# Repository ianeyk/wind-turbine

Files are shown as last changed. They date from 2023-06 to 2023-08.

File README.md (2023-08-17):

# wind-turbine
Working repo for summer research on the Just Energy Hub wind turbine design.

## GitHub Repo Index
* **Small_wind_turbine**
    * **3_phase_generator_buck_converter.plecs:** Main working PLECS model for the small turbine buck converter
    * **Frequency_analysis_buck_converter**
        * Contains four additional PLECS models which were used to run bode plots for designing the compensator circuit for the small wind turbine.
    * **Small_turbine_buck_converter_parameters**
        * **Buck_converter_parameters.ipynb:** Jupyter Notebook containing calculations for the inductor value and compensator circuit.
        * **Buck_converter_parameters.html:** Exported HTML of same Notebook
        * **Buck_converter_parameters.pdf:** Exported PDF of same Notebook
        * **Plecs_helper.py:** Library of helper functions used in the Notebook
    * **Small_buck_converter_design_calculations**
        * **Design_calculations.ipynb, html, pdf:** Secondary notebook for calculating such things as how much current the turbine can supply at safe rotation speeds, specs for the input capacitance value, slew rate to ensure the diff amps can respond fast enough, and resistor values for the indicator LEDs.
    * **KiCAD:** Contains the schematic and layout for the small-scale buck converter PCB board which I designed and manufactured over the summer.
* **Large_wind_turbine**
    * **siemens_model_buck_converter_v1.plecs:** Main working PLECS model for the large turbine buck converter, including the 1FW3208-1EE model of the physical generator. The only things that are different between this model and the small_wind_turbine model are the inductor value, compensator values, and perhaps the input capacitance.
     * **1_kv_3phase_generator_buck_converter.plecs:** Older model without using the 1FW3208-1EE model.
    * **Frequency_analysis_buck_converter**
        * Contains four additional PLECS models which were used to run bode plots for designing the compensator circuit for the large wind turbine.
    * **Large_turbine_buck_converter_parameters**
        * **Buck_converter_parameters.ipynb:** Jupyter Notebook containing calculations for the inductor value and compensator circuit.
        * **Minimum_conversion_ratio.ipynb:** Jupyter Notebook containing calculations for the minimum switching time given a 1kV-12V buck converter voltage ratio. I concluded that this is perfectly feasible given a 10kHz switching frequency.
    * **KiCAD:** Folder containing duplicates of the small wind turbine KiCAD files. I was going to start with a copy and modify it, but I never got around to starting it.
    * **LTspice:** Contains a single LTspice model verifying that the bootstrap gate driver will work.
* **Generic_wind_turbine**
    * Earlier exploratory work which served as a template for the above analyses. It should probably be moved to the Archive folder.
* **Measurements_and_calculations**
    * **Battery_measurements**
        * **Battery_resistance.ipynb, .html, .pdf:** Jupyter Notebook analyzing a small set of data I took on our 12V marine batteries in the lab to quantify the internal resistance.
    * **Generator_volage**
        * **Generator_voltage.ipynb, .html, .pdf:** Jupyter Notebook plotting the results of putting the small test turbine in front of the wind tunnel. It calculates the frequency and voltage amplitude at various wind speeds.
    * **Large_turbine_power_predictions**
        * **Large_turbine_power_predictions.ipyny, .html, .pdf:** Jupyter Notebook and exported versions analyzing the power generation data from one of the Eastern Wind Power documents as well as a PLECS model for the generator and the anemometer data from Olin's campus. I recommend a cut-out wind speed of 12m/s for the large turbine.
* **Charge_controller_code**
    * **Platformio.ini:** Platformio project for code running on the Adafruit Feather Adalogger board attached to the small-scale buck converter PCB I designed and manufactured this summer.
    * **src/main.cpp:** Main code file containing Arduino language to be uploaded to the Feather.
* **Archive**
    * **Generator_internal_resistance**
        * **Internal_resistance.ipynb, .html, .pdf:** Jupyter Notebook for an initial experiment determining the internal resistance of the small generator by hand-spinning the small turbine and watching the frequency and voltage decay as it slowed down. The internal resistance calculations match those in *Generator_voltage.ipynb*, and that notebook also has further relevant calculations. Hence this notebook is in the archive.

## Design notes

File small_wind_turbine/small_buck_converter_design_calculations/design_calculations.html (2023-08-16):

# Small Buck Converter Design Calculations¶

Author: Ian Eykamp, Date: 6/16/2023

## Purpose¶

To document certain calculations for the design of the small wind turbine buck converter, including

- Maximum output current
- Input capacitor size
- Slew rate of current wafeforms for speccing diff amps
- Indicator LED resistances

### Import libraries¶

plecs_helper.py is a file I created which defines some helper functions for nice plots and getting data off the oscilloscope and out of PLECS.

In [ ]:

import numpy as np
import pandas as pd
import matplotlib.pyplot as plt
import matplotlib.ticker as mtick
from UliEngineering.EngineerIO import format_value
from si_prefix import si_format
import plecs_helper as helper
%matplotlib
%matplotlib inline

# Imports and setup
from pint import UnitRegistry, Quantity
from scipy.signal import find_peaks
from scipy.optimize import fsolve

# pandas display using scientific notation
# pd.set_option('display.float_format', lambda x: f'{x:.3e}')

# use pint
units = UnitRegistry()
units.default_format = "~P.2f"

def to_decibels(arr, dc_gain = 0):
    return np.log10(np.abs(arr)) * 20 + dc_gain

Using matplotlib backend: TkAgg

## Calculating maximum current¶

The buck converter will draw a certain average current from the rectifier; in doing so, it produces a known output voltage (the battery voltage, which may be between 12V and 14.6V) and a known output current. The buck converter acts like an ideal transformer in that it preserves the product of voltage and amperage from the input to the output, $P_{in} = V_{in} \cdot I_{in} = V_{out} \cdot I_{out} = P_{out}$. The input voltage is the voltage between the terminals of the rectifier. Using this, we can calculate $I_{in} = V_{out} \cdot I_{out} / V_{in}$. Once we have $I_{in}$, we can calculate the voltage drop across the internal resistance of the generator by $V = IR$. I will call this $\Delta V_{internal}$. The voltage now available for the buck converter to use is $V_{in} = V_{gen} - \Delta V_{internal}$. So, depending on how much output current we want to draw into the battery, it will affect the voltage available at the buck converter input.

We need to charge a 12V battery (really, when it’s done charging, it will be at 14.6V) using our buck converter. Because of the chip we are using, our buck converter can have no more than a 50% duty cycle, which means our input voltage must be at least $2 \cdot 14.6V = 29.2V$ at a bare minimum. Round up to $V_{in} = 30V$ at a minimum.

To spin the generator and get power out of it, I will place it in front of the 4th floor wind tunnel in the Rocketry lab. Without getting to a point where I felt it was dangerous, I can get it to 30V with a 100Ω load resistance. I am confident I can spin it faster if we need a higher voltage; in fact, I made my design with 50V or higher in mind.

We know our voltage divider has to give us at least 30V from the 50V available. That means there can be no more than a 20V drop across the 14.5Ω internal resistance, which corresponds with a 1.3A current through the rectifier.

We have $I_{in} = 1.3A$, $V_{in} = 30V$, $V_{out} = 14.6V$, and $V_{in} \cdot I_{in} = V_{out} \cdot I_{out}$. Thus, the maximum current we can safely draw for a 50V generator voltage is 2.8A. Likely, the available current to the battery would be much smaller because the power converter is not 100% efficient (in fact 70% or 80% efficiency is a fairly good design) and because there are many auxiliary IC’s and the microcontroller that will eat up a lot of the excess current.

Well, I guess I’ll just keep our current down between 0 and 0.5A to be safe. (Just kidding, I already designed the thing with a maximum of 0.5A in mind, and I don't want to redo all the analysis after realizing that 1A or more would be fine).

In [ ]:

Vout = 14.6 * units.volt # battery voltage
Rinternal = 14.5 * units.ohm
Vgen = 50 * units.volt
Vin = 30 * units.volt
Vinternal = Vgen - Vin
Iin = Vinternal / Rinternal
Iout = Iin * Vin / Vout
print(f"Assuming Vgen = 50V, we have Iout = {Iout.to_compact(units.amp)}")

Assuming Vgen = 50V, we have Iout = 2.83 A

At 0.5A of output current, it would take only 35V at the generator, or actually probably closer to 40V because of the inefficiencies.

In [ ]:

Vout = 14.6 * units.volt # battery voltage
Rinternal = 14.5 * units.ohm
Vin = 30 * units.volt
Iout = 0.5 * units.amp + 0.5 * units.amp
Vgen = Vin + Iout * Vout / Vin * Rinternal
print(f"Assuming Iout = 0.5A, with another 0.5A for auxiliary components, we need Vgen = {Vgen.to_compact(units.volt)}")

Assuming Iout = 0.5A, with another 0.5A for auxiliary components, we need Vgen = 37.06 V

## Calculating Input Capacitance¶

This averaged transformer analysis has all been made possible by assuming the input voltage does not change in response to the switching

We have been calculating using the average input and output currents. For the buck converter to work properly, it needs to satisfy the input voltage even at the moment of peak current draw. In boundary conduction mode (BCM) where we are nominally operating, the peak current is two times the average current. For higher currents, we will go into continuous conduction mode (CCM), where the peak current is slightly less than twice the average current; for lower currents, we will go into discontinuous conduction mode (DCM) and require more than twice the average current at the peak.

Fortunately, if we have a big enough input capacitor, then we can smooth out the current waveform and almost exclusively care about the average current. By $I = C \frac{dV}{dt}$, there is always some voltage drop at the Vin node when the extra current is being sourced by the capacitor, but by choosing a large enough capacitance value, we can keep the voltage change to within +/- 1V of the average $\Delta V_{internal}$.

The source current follows a triangular waveform where it rises linearly from its starting current $I_{min}$ to $I_{peak}$ and then falls to zero. If we integrate this current over time, we get the total charge that is transferred during the upwards ramp as $\int_{t = 0s}^{D \cdot T_s} I_g dt = \frac{1}{2}T_s \cdot D \cdot (I_{peak} - I_{min}) + T_s \cdot D \cdot I_{min}$. If we are okay with rounding up by a factor of two, we can pretend the current is always $I_{peak}$, so that the charge becomes $Q = T_s \cdot D \cdot I_{peak}$. During this time, a current of $I_{avg} = \frac{I_{peak}}{2}$ is always being sourced by the generator, which over the switching cycle is $Q = T_s \cdot D \cdot \frac{I_{peak}}{2}$. So our capacitor only needs to source the other $T_s \cdot D \cdot \frac{I_{peak}}{2}$ of the charge, all while depleting only 1V of its voltage.

In reality, the charge required is about half of that value for CCM and BCM and has a limit approaching that value as we go deep into DCM.

We have $C = \frac{Q}{V}$, so we have $C_{input} = \frac{T_s \cdot D \cdot \frac{I_{peak}}{2}}{1V}$

In [ ]:

Fs = 50 * units.kilohertz
Ts = 1 / Fs
D = 0.36
Ipeak = 1 * units.amp
Vripple = 1 * units.volt

Cinput = Ts * D * Ipeak / 2 / Vripple
print(f"Cinput = {Cinput.to_compact(units.farad)}")

Cinput = 3.60 µF

So yeah, 10uF should be about enough.

## Calculating Diff Amp Slew Rate Across Shunt Resistors¶

(To ensure our diff amps are fast enough to measure the current waveforms)

The slope of the current waveform over time is linear and determined by the inductance value we chose for the inductor, $V_L = L \cdot \frac{dI}{dt}$, where $V_L = V_g - V_{bat}$, so $\frac{dI}{dt} = \frac{(V_g - V_{bat})}{L}$. We chose the up-going slope because it is necessarily steeper than the down-going slope because we are limited to a <50% duty cycle. This tells us the rate of current rise across the first shunt resistor. Due to the low-pass filtering of the capacitor, the rate of rise of the second shunt resistor will be smaller. For a given rise in current $\Delta I$, the voltage across the shunt resistor will rise by $\Delta V = \Delta I \cdot R_{shunt}$. Therefore, the slew rate of the voltage rise across the shunt resistor will be $\frac{dV_{shunt}}{dt} = \frac{dI}{dt} \cdot R_{shunt} = \frac{(V_g - V_{bat})}{L} \cdot R_{shunt}$.

In [ ]:

Rshunt = 50 * units.milliohm
Vg = 40 * units.volt
Vbat = 12 * units.volt
L = 345 * units.microhenry
dIdt = (Vg - Vbat) / L * Rshunt
print(f"Slew rate = {dIdt.to(units.volt / units.microsecond):.2e}")

Slew rate = 4.06e-03 volt / microsecond

Shunt resistor power rating

In [ ]:

Ipeak = 2 * units.amp
Rshunt = 10 * units.milliohm
shunt_resistor_power_rating = Ipeak ** 2 * Rshunt
print(f"Shunt Resistor Power = {shunt_resistor_power_rating.to_compact(units.watt):.2f}")

Shunt Resistor Power = 40.00 milliwatt

## LED resistor calculations¶

3 voltage levels: 15V, 5V, and 3.3V 2V forward voltage across LEDs 30mA maximum DC current, aiming for 10mA

In [ ]:

V1 = 50 * units.volt
V2 = 5 * units.volt
V3 = 3.3 * units.volt
VF = 2 * units.volt
Idesired = 10 * units.milliamp

R1 = (V1 - VF) / Idesired
R2 = (V2 - VF) / Idesired
R3 = (V3 - VF) / Idesired
print(f"R1 = {R1.to_compact(units.ohm):.2f}")
print(f"R2 = {R2.to_compact(units.ohm):.2f}")
print(f"R3 = {R3.to_compact(units.ohm):.2f}")

R1 = 4.80 kiloohm
R2 = 300.00 ohm
R3 = 130.00 ohm

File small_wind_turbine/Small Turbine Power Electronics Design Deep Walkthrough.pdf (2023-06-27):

## Small Turbine Power Electronics Design

Author: Ian Eykamp
Date: June 27, 2023

Purpose:

This document is a detailed design description for the power electronics for the small wind turbine. My work so far consists of several PLECS models, a KiCAD schematic and layout (coming soon), and an LTspice simulation. After review, this design will be manufactured on a PCB and validated by testing on the small wind turbine. Ideally, the same circuit can be scaled up for use on the large wind turbine, with bulkier components.

GitHub repo containing all files: https://github.com/ianeyk/wind-turbine

Main folder for this project: https://github.com/ianeyk/wind-turbine/tree/main/small_wind_turbine

Link to KiCAD schematic: https://github.com/ianeyk/wind-turbine/tree/main/small_wind_turbine/KiCAD/small_wind_turbine

Link to PLECS Model: https://github.com/ianeyk/wind-turbine/blob/main/small_wind_turbine/3phase_generator_buck_converter.plecs
Compensator design notebook with simulations:

https://github.com/ianeyk/wind-turbine/blob/main/small_wind_turbine/small_turbine_buck_converter_parameters/buck_converter_parameters.ipynb

Overview:

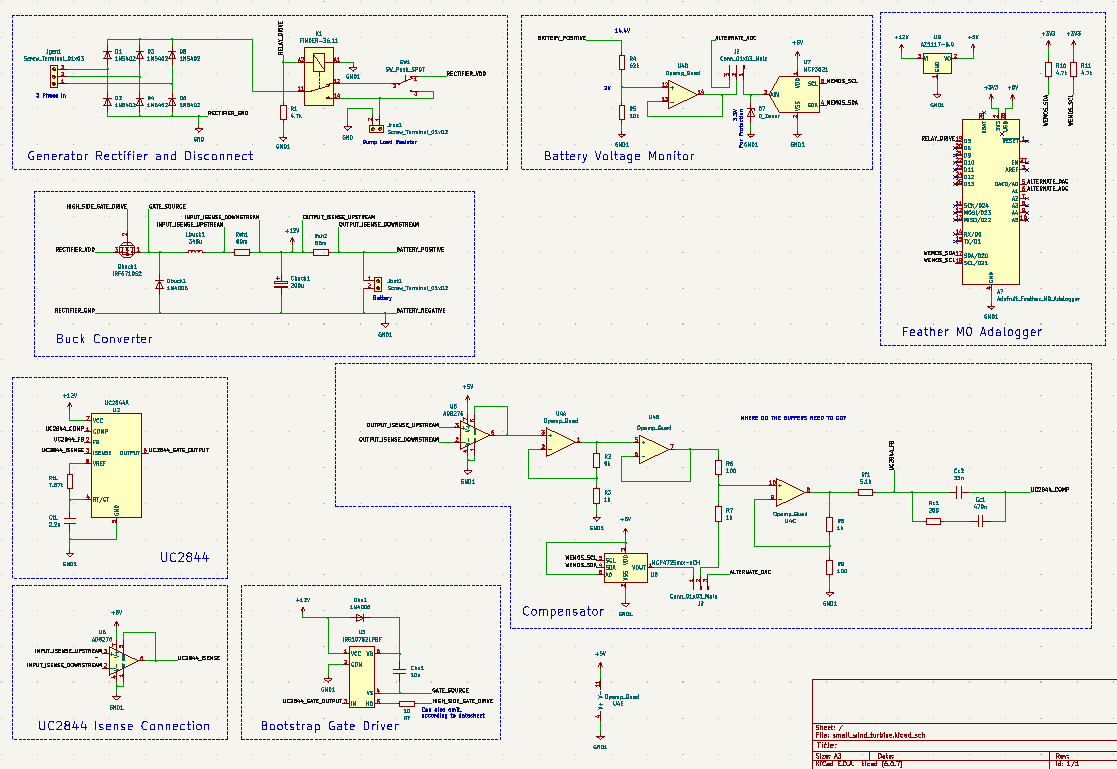
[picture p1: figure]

The circuit consists of a 3-phase rectifier with disconnect circuitry, the buck converter circuit, compensator circuit with adjustable current control, UC2844 with auxiliary current sense and gate driver ICs, and a microcontroller for monitoring the battery level and specifying the charging current.

Generator

The generator sits at the base of the small vertical axis wind turbine. It outputs 3-phase power when the turbine is spun. See this slideshow (https://docs.google.com/presentation/d/1cCFfezFgubyGQrMmF5VYWpKT9RvoXpGWEBQokzURn6g/edit) on how 3-phase power works. The three wires from the generator connect into the Jgen1 terminal on the PCB.

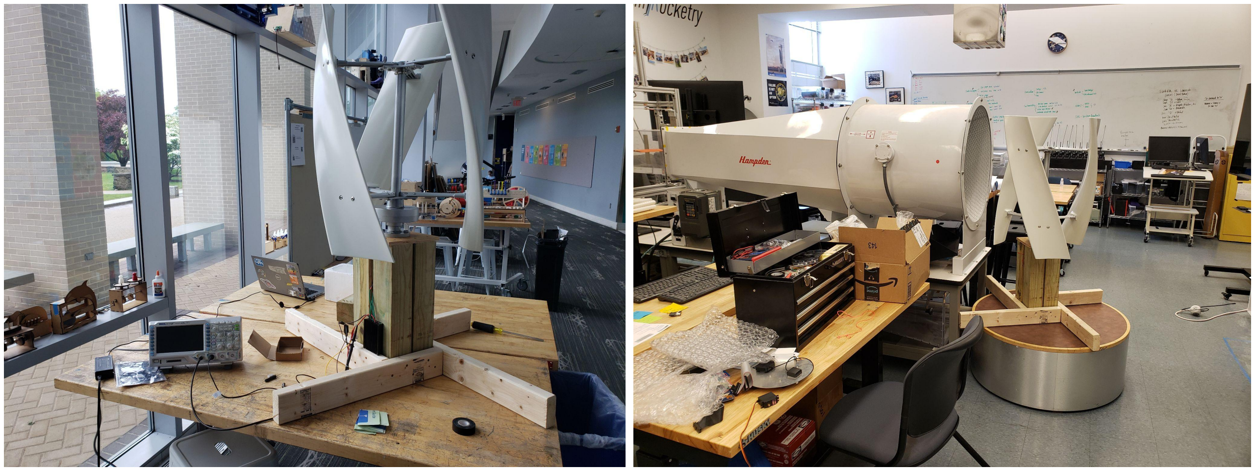
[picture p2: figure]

The generator has an internal resistance of 14.5Ω, which can be modeled with a resistor in series with each of the three phases. In larger generators, the inductance of the coils is also important, but here I have assumed the inductance is zero. It is important to know the internal resistance, because it determines how much current we are able to draw from the generator at a given voltage, as follows.

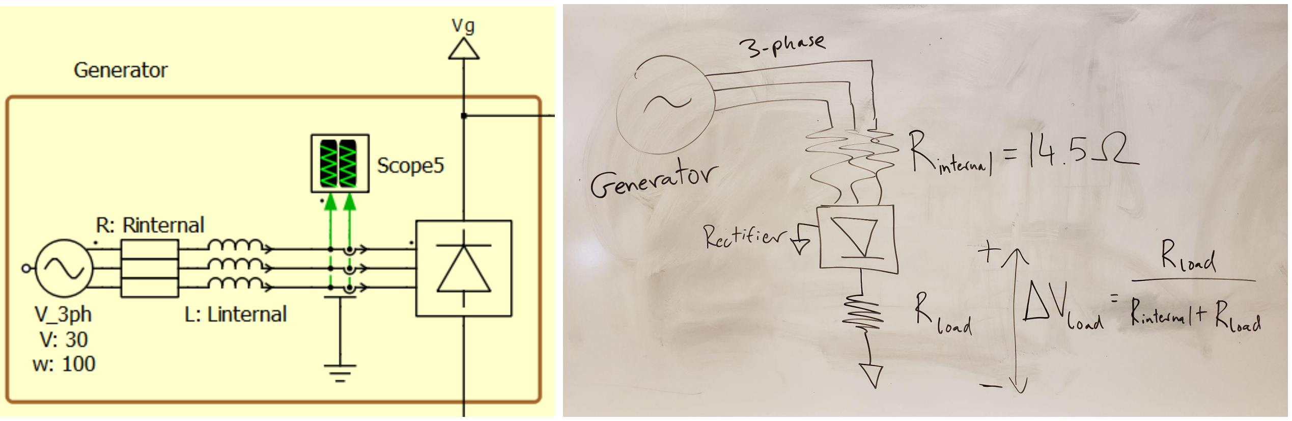
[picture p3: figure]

No matter what its form, everything to the right of the rectifier can be treated as a load resistor with an impedance equal to R = V / I. This is true for our circuit, where we are charging a battery at a certain voltage (12V) with a certain current (0.25A). Our output impedance is 48Ω. The load impedance and the internal resistance form a voltage divider, such that we only experience

across the load, which in this case is the inputs to our buck converter.

We need to charge a 12V battery (really, when it’s done charging, it will be at 14.6V) using our buck converter. Because of the chip we are using, our buck converter can have no more than a 50% duty cycle, which means our input voltage must be at least 2 * 14.6V = 29.2V at a bare minimum. Round up to 30V.

To spin the generator and get power out of it, I will place it in front of the 4th floor wind tunnel in the Rocketry lab. Without getting to a point where I felt it was dangerous, I can get it to 30V with some load resistance. I am confident I can spin it faster if we need a higher voltage.

For the circuit design, I assume the generator voltage is nominally 30V on each wire, but that
means the rectified voltage is | , because the rectifier takes the maximum
difference between any two wires. Again, see this slideshow. (https://docs.google.com/presentation/d/1cCFfezFgubyGQrMmF5VYWpKT9RvoXpGWEBQokzURn6g/edit) So our voltage divider has to give us at least 30V from the 50V available. That limits the output impedance we are allowed to have to somewhere around 25Ω (after conservative rounding). We know our output voltage will be >12V, so by I = V / R = 12V / 25Ω, our output current should not greatly exceed 0.5A. Excellent. I designed with a quarter of an amp in mind.

Rectifier and shut-off switches

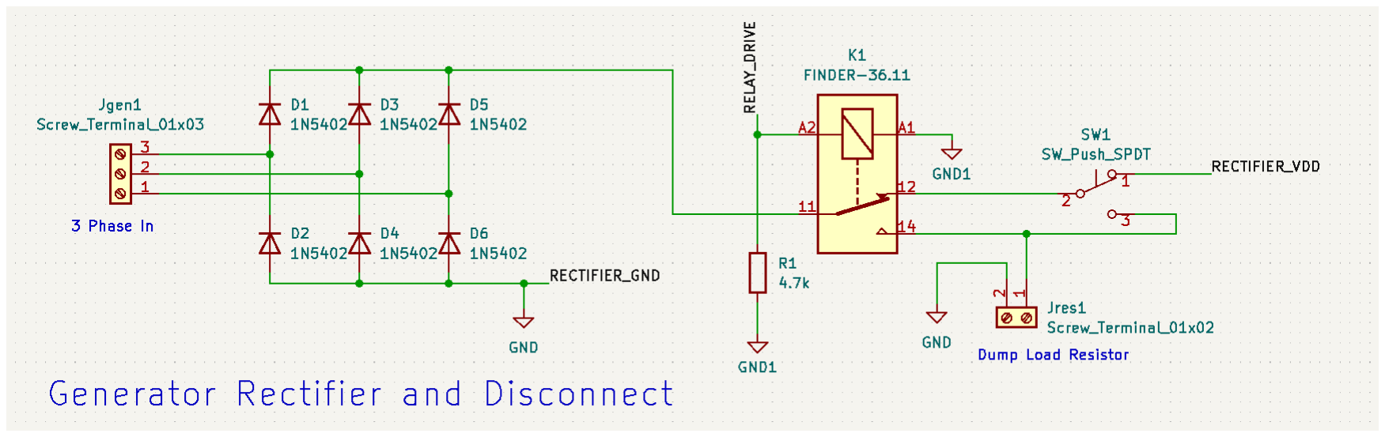
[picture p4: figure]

The rectifier is also explained in the slideshow (https://docs.google.com/presentation/d/1cCFfezFgubyGQrMmF5VYWpKT9RvoXpGWEBQokzURn6g/edit) mentioned previously. I use Schottky diodes with the lowest forward voltage drop I could find for these diodes, to avoid dropping the voltage too much during rectification. A smaller voltage drop also means less power will be dissipated, since all of the current passes through these diodes.

Next is a relay in series with a manual switch. The relay is essentially a switch that is controlled by the microcontroller to shut off current when the battery is charged or in case something goes wrong. The manual switch serves the same purpose. It can be seen from the schematic that if either of these switches is opened, the current will flow through a dump resistor instead, electronically braking the turbine. The dump resistor is separate from the PCB and will be connected via a plug-in terminal.

The dump resistor will be 16Ω to match the generator internal resistance and rated for 300W, with its own heat sink. That should be more than enough for a 50V input, even if all the power is dissipated through the dump load and not through the internal resistance. We have

. At 70V, we have 306W, but again some of the power will be dissipated by the internal resistance.

A relay and manual switch are chosen which can easily handle the high voltages and currents.

Buck Converter

The best way to understand the buck converter is to take Power Electronics with Beat. Failing that, here is a crude explanation.

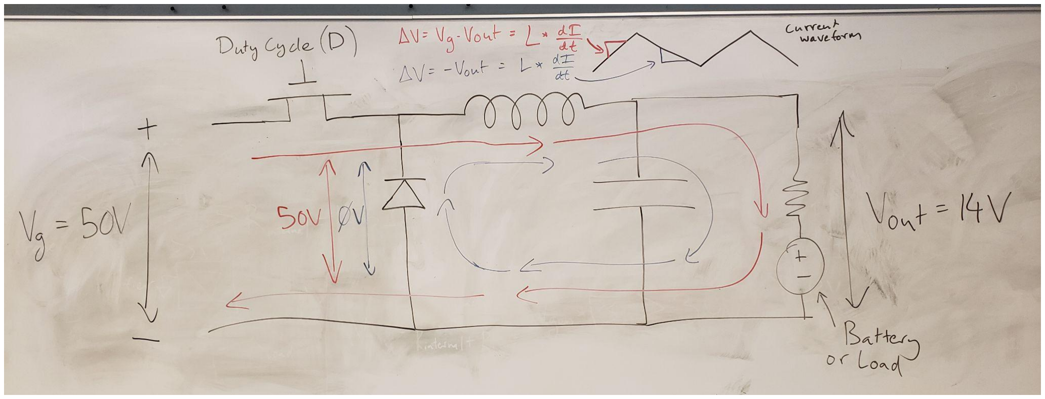
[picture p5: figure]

A buck converter consists of four primary components: a MOSFET which acts like a switch, an inductor, a diode, and a capacitor. The MOSFET is driven with a certain duty cycle that determines the voltage conversion ratio (Vout / Vg). It’s easiest to analyze if we assume Vout is fixed at the desired voltage; in fact, this is the primary role of the capacitor. We choose a large enough capacitor (in our case, 200uF) so it can smooth out any bumps or discontinuities in the output voltage, of which there will be plenty.

During the time when the switch is on, current flows from the source through the inductor to the output (red arrows), ignoring the diode. Assuming the output is at constant voltage and the MOSFET is a perfect conductor, there must be a voltage drop across the inductor of VL = Vg

Vout. The inductor obeys the law VL = L dI/dt; VL

is constant, so the current increases linearly. It does so until the switch is turned off.

When the switch is off, no current flows from or to the source. An inductor cannot instantaneously change its current, so current continues to flow through the inductor and into the load (blue arrows). Since it can’t flow back to the source terminals, current now flows through the diode to complete the loop. Assuming the output voltage is still constant and there is no voltage drop across the diode, the voltage across the inductor is now -Vout (it’s negative because the left side of the inductor is now at a lower voltage than the right hand side). As it discharges, the current through the inductor decreases by VL = L dI/dt, where VL = -Vout. In our case, we turn the switch on again before the inductor gets to zero current (continuous conduction mode, or CCM), but there are plenty of times you want the current to fall all the way to zero and stay there a while before the cycle repeats (discontinuous conduction mode, or DCM). In either case, the capacitor is large enough to ensure the output voltage stays at the average value the entire time.

Another way to think about the buck converter is just as a switch turning on and off really fast, the way you can control the brightness of an LED with PWM. The ratio of input to output voltages is controlled by the duty cycle of the switch. Then the inductor and capacitor act as a massive low-pass filter on the output.

UC2844

The UC2844 is an integrated circuit (IC) for controlling the duty cycle of power converters like this one. We gained a lot of familiarity with it in Power Electronics. Here is the datasheet for the newest version, the UC2844A. (https://www.ti.com/lit/ds/symlink/uc2844a.pdf)

The way it works is it takes in a voltage at the ISENSE pin corresponding with the amount of current through the inductor—typically, the voltage across a known shunt resistance is used. In my case, since my shunt resistor is not connected to ground on one side, I have to take the voltage difference using a differential amplifier (diff amp).

In the last section, I described how the voltage through the inductor increases linearly while the switch is on. Once the ISENSE pin reaches the threshold voltage, the UC22844 turns the switch off and waits a specified amount of time before it turns it back on again. The amount of time it waits is determined by Rt1 and Ct1, and I chose values that will make it turn on every 0.00002 seconds, or at a frequency of 50kHz. By choosing the threshold for the ISENSE pin at which it turns the switch off, we can set the duty cycle of the switch and thus the voltage conversion ratio.

Instead of setting the threshold voltage directly, I am using a feedback loop to adjust the threshold until it reaches a desired output current into the battery that is specified by the microcontroller. This feedback loop is made stable by the compensator described in the next section.

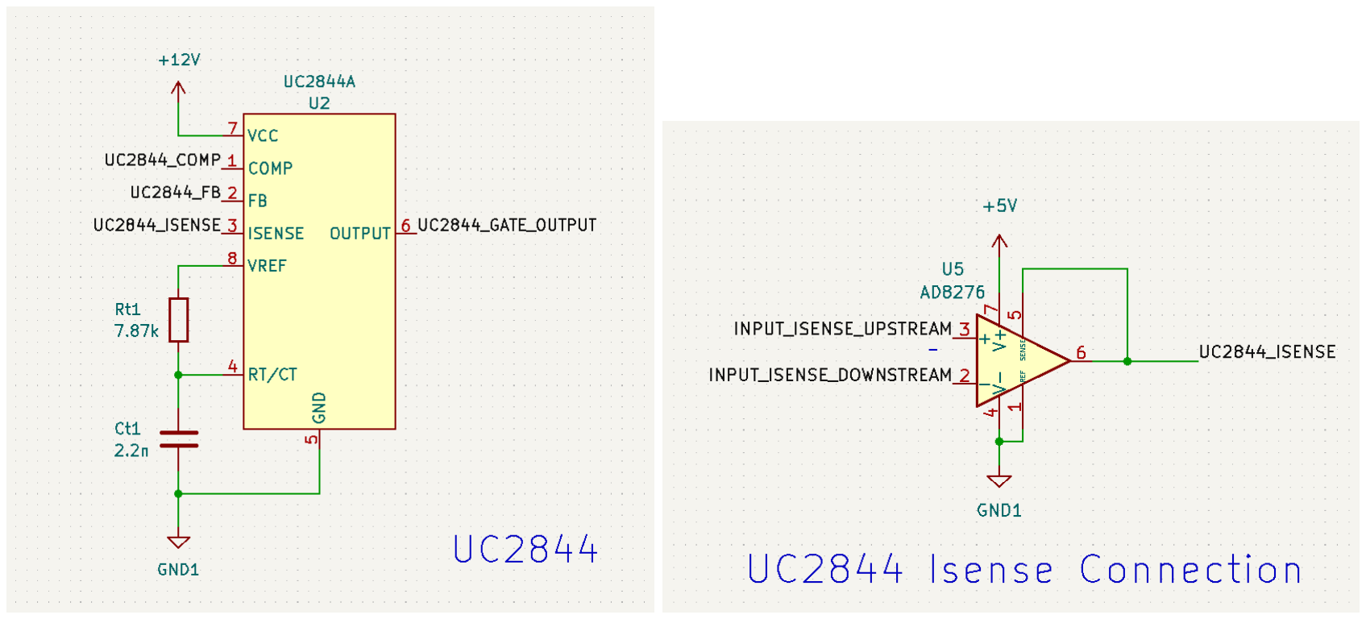
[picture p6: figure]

Compensator

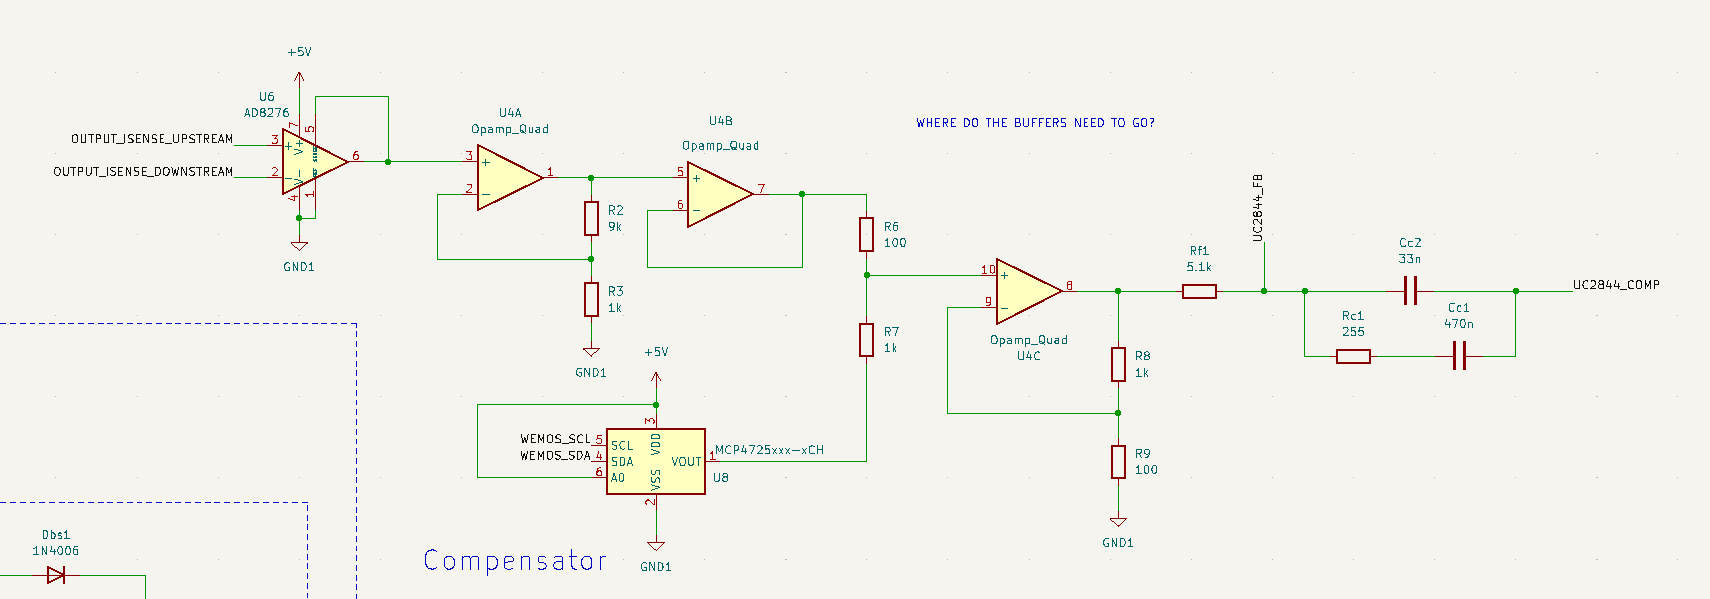
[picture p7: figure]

The actual compensator that we learned how to design in Power Electronics is the rightmost part of this circuit, comprising Rf1, Rc1, Cc1, and Cc2. Its job is to ensure that the feedback loop is stable and has a unity gain at steady-state; that is, if we give it a constant target value, then we want it to settle on exactly that value. The rest of this circuit is essentially used to specify the target value.

Specifically, based on the internal design of the UC2844, the target value is defined as the input quantity that makes the value of the UC2844_FB pin equal to 2.5V. If the input quantity is such that the UC2844_FB pin is higher than 2.5V, then it will decrease the duty cycle; and if the UC2844_FB pin is lower than 2.5V, it will increase the duty cycle. I’m using the term ‘input quantity’ because it really can be anything—in Power Electronics, the input quantity was the load voltage after going through a 4:1 voltage divider; thus, the target value was a 10V load voltage, such that the UC2844_FB pin was 2.5V.

In our case, the target value is a load current of between 0 and 0.5A, as specified by the microcontroller. Here’s how:

Suppose we have a 0.5A current going into the load, which in this case is our battery. The current passes through a shunt resistor Rsh2, creating a voltage drop between nodes OUTPUT_ISENSE_UPSTREAM and OUTPUT_ISENSE_DOWNSTREAM. Rsh2 is 50mΩ, which means the voltage difference is V = 50mΩ * 0.5A = 25mV. This is picked up by the diff amp and amplified 10-fold by the first op-amp. R5 and R7 form a linear voltage combiner (aka a voltage adder), whereby the top signal is multiplied by a further 10-fold and added to the bottom signal. Assume the bottom signal is 0V for now. So we just had a 100-fold gain on our 25mV, which indeed yields 2.5V for a current of 0.5A.

The bottom signal comes from a digital to analog converter (DAC) controlled by the microcontroller. Suppose we set this to 1.25V. Then the voltage adder will add up to 2.5V if and only if the top signal is also equal to 1.25V. This corresponds to an input voltage of 0.25A. By setting the DAC value to any value between 0V and 2.5V, we can set the target current to be anywhere between 0A and 0.5A. This is useful, because as the battery gets closer to full charge, we will want to reduce the current flowing into it and eventually stop charging it altogether.

I used two stages of amplification each with a gain of 10 instead of one stage with a gain of 100, because I had extra op-amps (I’m using an op-amp quad package), and I figured it might be more accurate. I do not know if all the buffering is necessary or whether I need another buffer on the output before the compensator components. Also, all the op-amps and the diff amp are powered by 5V, which is taken by a linear regulator from the battery. Yet I am using the diff amp to measure voltages which are nominally 12V-14.5V or so. Fortunately, the particular diff amps (https://www.analog.com/media/en/technical-documentation/data-sheets/AD8276_8277.pdf) I’m using are rated to measure voltages beyond their power supply rails and significantly above 15V.

When analyzing the compensator circuit, it helps to look at the functional block diagram of the UC2844. In particular, there is an op amp with UC2844_FB leading to the inverting input, UC2844_COMP leading to the output, and the noninverting input internally tied to 2.5V.

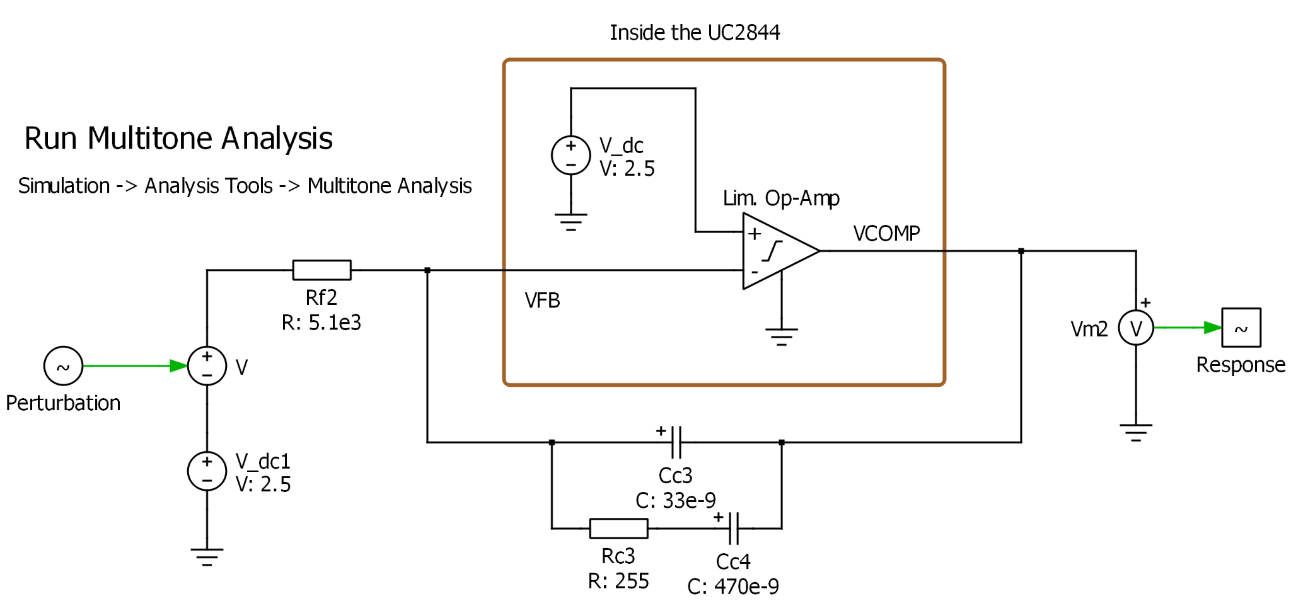
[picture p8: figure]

Choosing Compensator Values

This is the subject of an extensive analysis documented in this jupyter notebook, (https://github.com/ianeyk/wind-turbine/blob/main/small_wind_turbine/small_turbine_buck_converter_parameters/buck_converter_parameters.ipynb) using this PLECS model (https://github.com/ianeyk/wind-turbine/blob/main/small_wind_turbine/3phase_generator_buck_converter.plecs) and other resources in this folder. (https://github.com/ianeyk/wind-turbine/tree/main/small_wind_turbine) The idea is to analyze the transfer function of the plant, which looks like this…

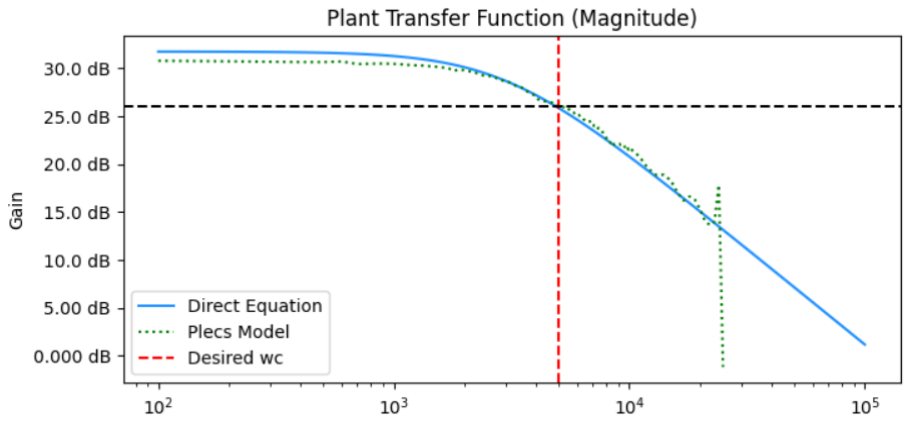
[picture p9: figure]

…and make it suitable for stable feedback with no DC offset. This is done by adding another transfer function—the compensator—in series, whose transfer function looks like this…

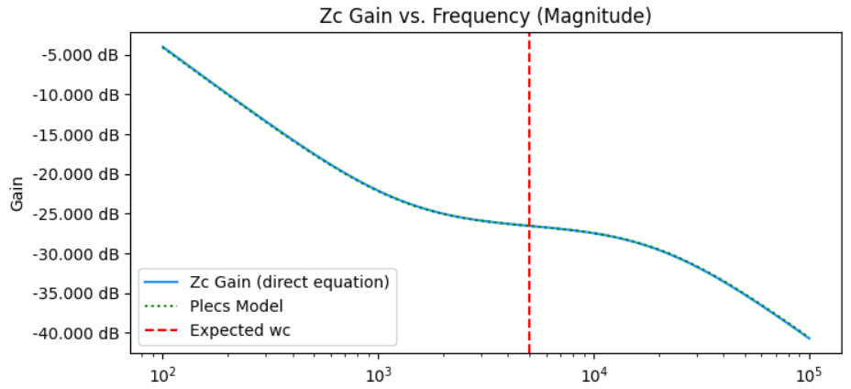
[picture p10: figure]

…to produce a net transfer function with infinite gain at DC, zero gain at the red dashed line, and strong attenuation near the switching frequency, such that any fluctuations due to the switching behavior are ignored. After closing the feedback loop, the transfer function becomes…

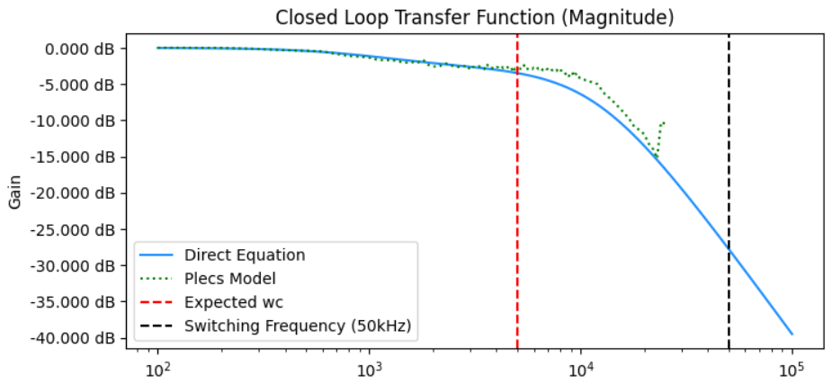
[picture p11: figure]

…which has all the properties described. Here, the black dashed line is the switching frequency, and it has attenuation of around -30dB, whereas at steady-state (0Hz), there is unity gain, meaning the system will reach the desired state if we feed it a steady target value.

The PLECS model verifies that the target current can be arbitrarily specified by the microcontroller between 0A and 0.5A, and the output current will settle on that value within half a millisecond with no overshoot.

Placement of the current sense resistors

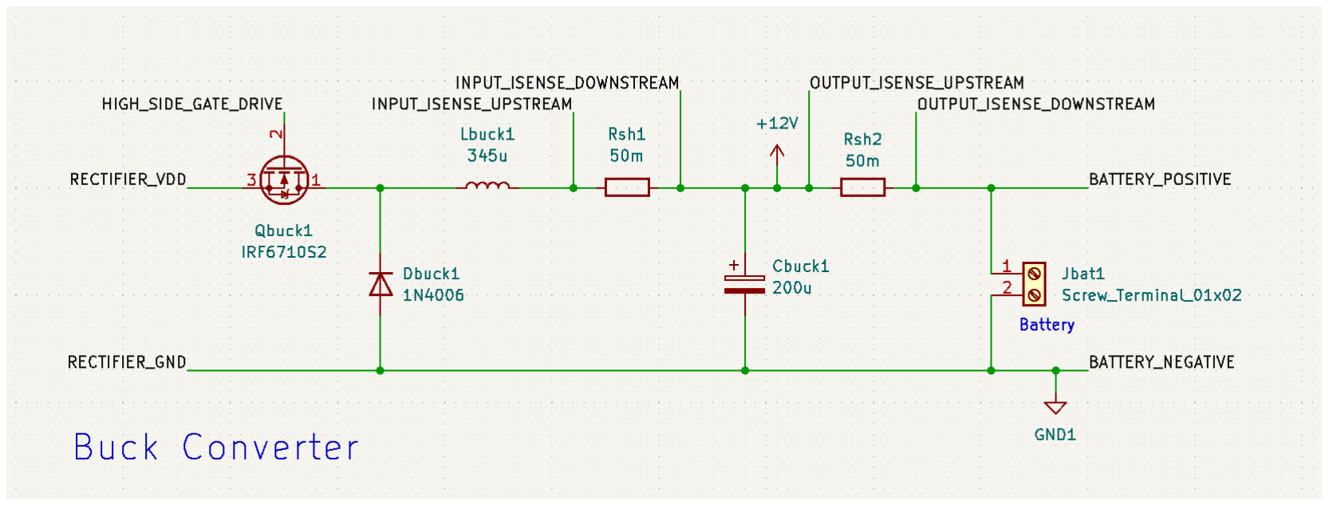
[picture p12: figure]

A current sense resistor is essentially a shunt resistor whose resistance is small and well known, such that when current passes through it, the current can be inferred from the voltage drop by I = V / R. In Power Electronics, we placed the current sense resistor downstream of the load, with its negative lead at ground. This worked because it was easy to measure the shunt voltage, as it was already referenced to ground. The MOSFET was also tied through the shunt resistor to ground. Contrarily, my design establishes a common ground between the load (the battery) and the source (the negative rectifier terminal) by moving the MOSFET and the shunt resistors to the high side.

I already established that we can use a diff amp to measure the voltage difference across the shunt resistors, even though the nominal voltage is on the order of 12-15V. But why are there two of them, and why these specific locations?

The first shunt resistor, Rsh1, acts as the current sense pin tied to UC2844_ISENSE, which is directly responsible for making the UC2844 turn off the MOSFET when the duty cycle is reached. It is critical that the resistor used for this purpose be placed to the left of the 200uF capacitor. If it is to the right, then some of the current will flow through the parallel path through the capacitor, and it will not trigger the current threshold at the proper time. PLECS simulations show that the output is unstable and sporadic when the UC2844_ISENSE resistor is to the right of the capacitor.

The second shunt resistor, Rsh2, is directly in series with the battery, such that the resistor current is equal to the battery current. This is the current sense resistor that is used to feed the compensator and feedback loop. I specify that I want a certain current, say 0.25A, going into the battery, and I want the feedback loop to adjust until I get that amount of current into the battery, regardless of how much current is drawn by the auxiliary components or dissipated by anything along the way.

The +12V rail is used for powering the UC2844 and gate driver IC directly, as well as passing through a linear regulator to supply 5V to the microcontroller, op-amps, diff amps, and other components. Notably, the 12V rail is supplied upstream of the second shunt resistor, such that as much current can be siphoned off as is needed without affecting the current to the battery controlled by the feedback loop. This is modeled by a 125mA current sink upstream of the second shunt resistor in my PLECS model.

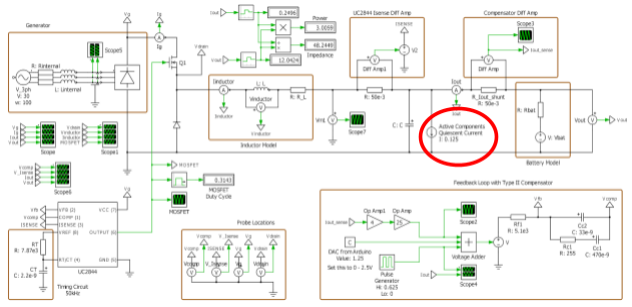
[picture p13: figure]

The +12V supply rail

It should be noted that the +12V rail symbol used in KiCAD is not actually 12V. Instead, it is the battery voltage which is dependent on its state of charge, and it will be closer to 14.6V or 15V when the battery is nearly charged and there is still some current going through Rsh2.

Battery voltage monitor

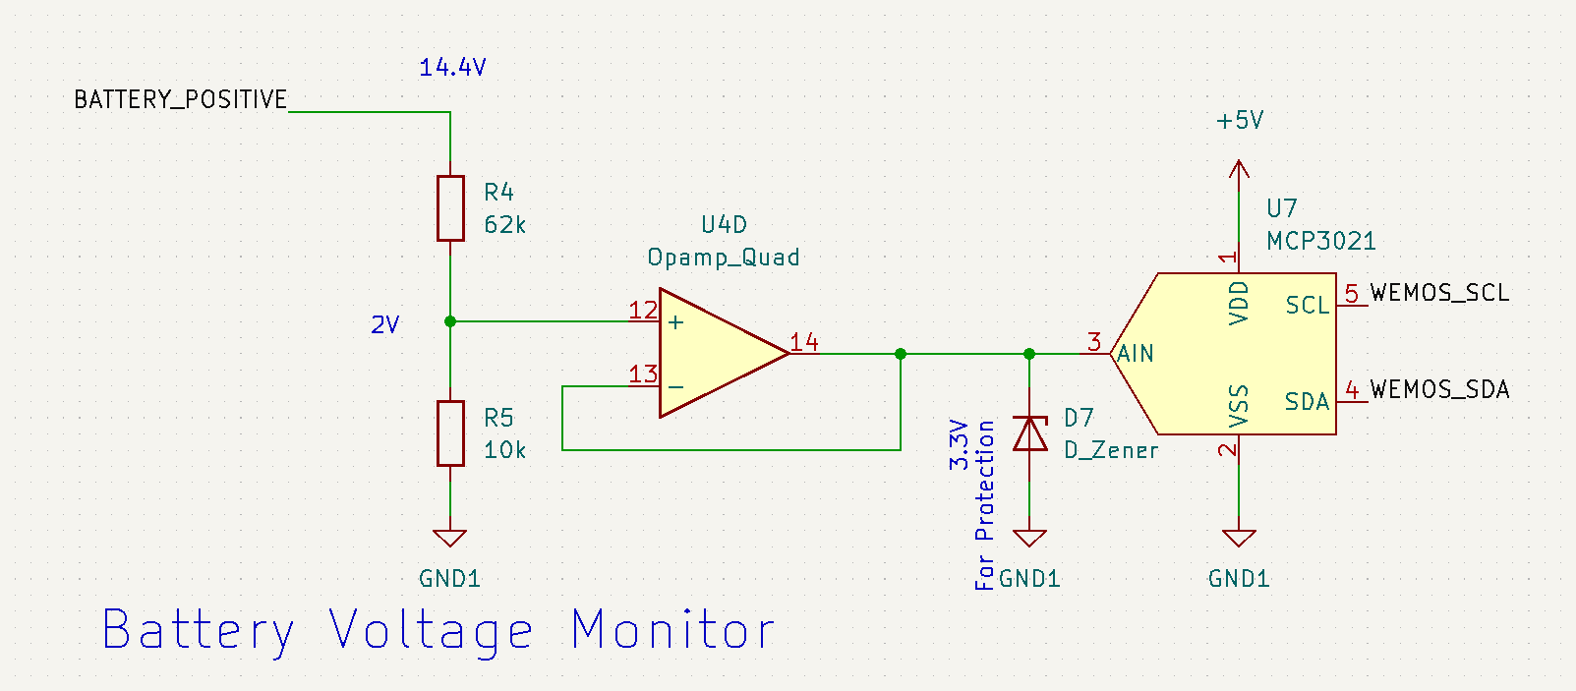
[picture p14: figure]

The state of charge of the battery can be monitored based on its voltage. Sources (https://www.westmarine.com/west-advisor/Selecting-a-Battery-Charger.html) recommend charging the battery at a high current up to 14.4V or 14.6V, and then reducing the current for the remainder of the charging cycle. Thus, it is important to know the battery voltage accurately and precisely.

For this, a simple resistive divider is used to divide the 12V-14.6V voltage down to the 0-3.3V range so it can be accessed by an analog to digital converter (ADC). The ADC is sensitive to overvoltage at the input, and the voltage should never need to go above 3.3V, so I included a zener diode for safety. It is probably not necessary.

I am using an external ADC and DAC. These are usually available onboard a typical microcontroller using the analog pins, but I don’t trust those to be accurate all the time. The ADC and DAC are accessible to the microcontroller via I

2C communication. I included 4.7kΩ pull-up resistors on the I

2C lines.

Bootstrap Gate Driver

I mentioned earlier that I moved the MOSFET of the buck converter circuit from the low side (downstream of the load and closest to ground) to the high side (upstream of the inductor) for the purposes of a shared ground between the battery and the rectifier. The low side MOSFET could be easily switched using the UC2844 gate drive output, which in this case would be nominally 12V. Since the MOSFET source was tied close to ground, the gate-to-source voltage could easily be made high or low.

Using a high-side MOSFET presents the tricky problem that when the MOSFET is conducting, its source is nearly at Vg, which is close to 50V. In order to drive the gate, we need a gate driver capable of delivering at least 60V to the gate; or rather, 10V between the gate and the source.

Fortunately, we have the bootstrap circuit which accomplishes exactly this, along with a purpose-built IC (https://www.analog.com/media/en/technical-documentation/data-sheets/4440fb.pdf) to serve as the high-side gate driver.

It works by maintaining an almost constant voltage across the capacitor due to the diode, with the negative terminal of the capacitor connected to the source of the MOSFET. Consider the relation I = C dV/dt, where I can only flow forward through the diode. The capacitor cannot decrease in voltage except through parasitics or by discharging into the gate capacitor on the MOSFET. As the capacitor’s voltage degrades over time, it will be replenished every time its positive lead drops below 12V, which happens every cycle of the buck converter when the switch is turned off and the source of the MOSFET is tied close to 0V. When the MOSFET is turned on and its source rises close to 50V, the voltage across the capacitor means the gate drive pin is around 60V as desired.

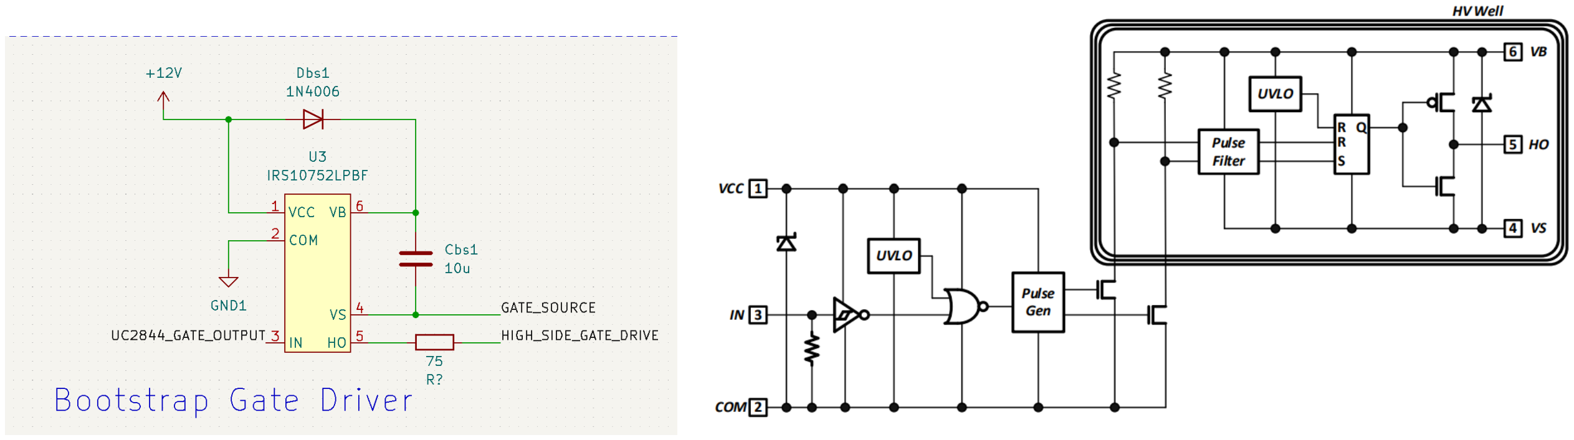
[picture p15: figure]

The image on the right shows the block diagram of the gate driver IC and how it converts a low logic level voltage into a high voltage output.

The gate driver is capable of pushing 2.4A out the high side pin. According to the datasheet, this is enough current that you don’t even need a gate drive resistor. I will put a 10Ω resistor in series just in case. This gate driver can handle up to 75V or 80V continuous current, so it may be a limiting factor if we want to crank up the turbine power a whole bunch, but we shouldn’t need to. I found another IC (https://www.infineon.com/dgdl/irs10752lpbf.pdf?fileId=5546d462533600a40153567308ca276d) we can use which goes up to 120V, but it can only drive 260mA worth of current, which will increase the switching time. It is critical to make the switching time as short as possible, because this is a leading cause of power dissipation in switching power converters, as we learned in Power Electronics.

I have verified in LTspice the behavior of the diode-capacitor circuit and confirmed that it can boost a high voltage level even higher for short periods of time, even when a small parasitic current is constantly being pulled from that node. 10uF should be way more than enough for the bootstrap capacitor.

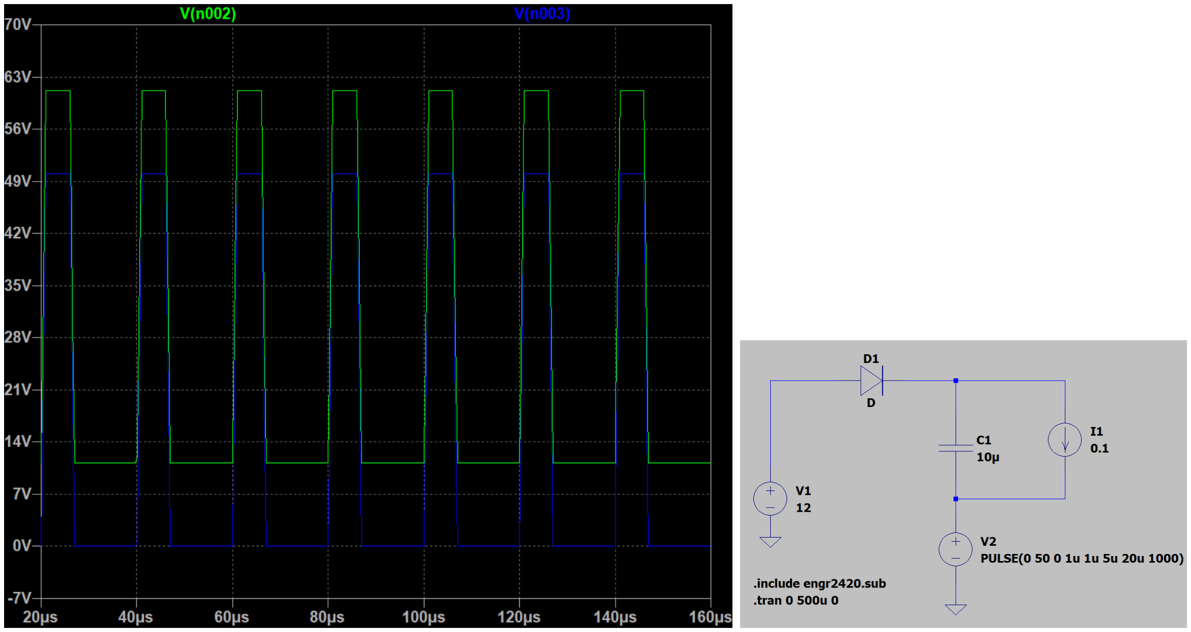
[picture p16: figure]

Microcontroller

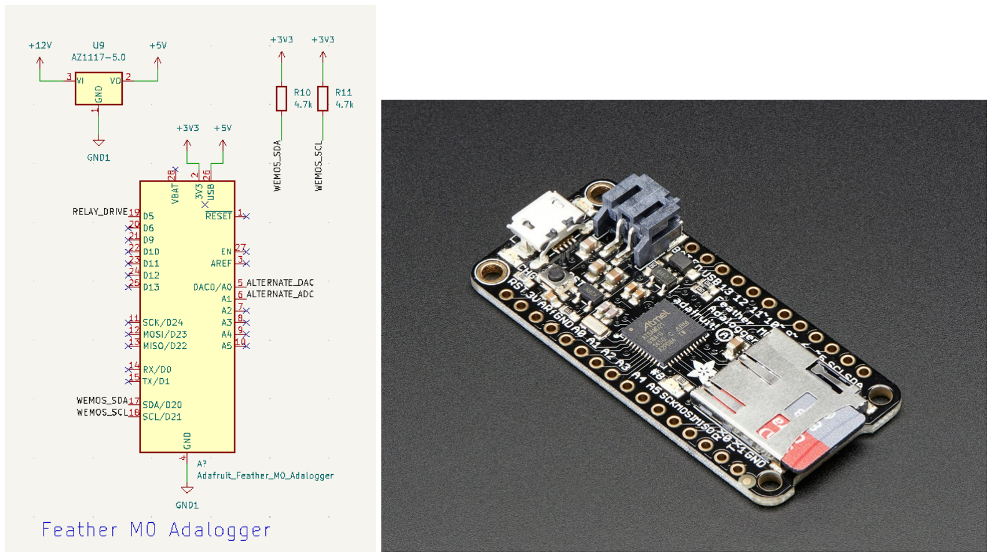
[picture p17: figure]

The PCB will have two rows of female sockets where an Adafruit Feather M0 Adalogger board can be plugged in. The Feather will be powered via the Vin pin using the 5V linear regulator on the PCB. It will also have breakout pins for attaching other sensors. The Feather seems like a user-friendly, reliable microcontroller with an SD card reader built in. This could be useful for obtaining data on the state of charge of the battery over time to determine the optimal charging current.

The main connections to the microcontroller are the I

2C pins for the DAC and ADC, as well as one digital pin for controlling the relay. I also have jumpers that will let us bypass the external DAC and ADC and use the built-in ones on the Feather instead. It will be programmed to monitor the battery voltage using the ADC and to follow a specified charging current curve for the battery. If dangerous conditions are detected, it will shut off power to the circuit using the relay at the buck converter’s input.

When the battery is attached, it should be able to feed the 5V regulator and continue to power the microcontroller, allowing it to reconnect the relay if it is given the signal to resume charging.

Things to do:

Add input capacitors on the voltage supply pins of all the IC’s
Add fuses
Add test points

Add indicator LEDs

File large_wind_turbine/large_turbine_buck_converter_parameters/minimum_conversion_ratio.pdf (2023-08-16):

# Minimum Buck Converter Voltage Conversion Ratio Calculation

### Author: Ian Eykamp, Date: July 11, 2023

# Purpose

To determine whether a 1kV to 12V buck converter is possible.

# Methodology

According to this document, (https://www.ti.com/lit/an/slyt293/slyt293.pdf) the lower bound on the buck converter's voltage conversion

### ratio is driven by the minimum on time , which has to do with the controller's ability

to react in time to a quickly rising current. This will affect the controller's minimum possible duty cycle.

For a given | , we can have a duty cycle of | , where | is the switching
period.

This can be confirmed by looking at the inductor's curent waveform. On the inductor rising
edge, we have | lasting | , and on the falling edge, we have
lasting | . Solving for

### gives

, as expected.

Ton,min

Ton,min

Ton,min
Ts

Ts =

1
Fs

=

dIrise
dt

(Vg−Vout)

L

Ton,min

= −

dIfall

dt

Vout
L
Ts − Ton,min | ⋅ Ton,min = − | ⋅ (Ts − Ton,min)

dIrise
dt

dIfall

dt

⋅ Ton,min = | ⋅ (Ts − Ton,min)

(Vg⁻Vout)

L

Vout
L

(Vg − Vout) ⋅ Ton,min = Vout

⋅ (Ts − Ton,min)

Vg ⋅ Ton,min − Vout ⋅ Ton,min = Vout ⋅ Ts − Vout ⋅ Ton,min

Vg ⋅ Ton,min = Vout ⋅ Ts

=

Ton,min
Ts

Vout
Vg

In [ ]:
import numpy as np
import pandas as pd
import matplotlib.pyplot as plt
import matplotlib.ticker as mtick
from UliEngineering.EngineerIO import format_value from si_prefix import si_format
import plecs_helper as helper
%matplotlib
%matplotlib inline

Using matplotlib backend: TkAgg

Minimum duty cycle given Tmin_on = 600.00 ns is D = 0.006
Desired duty cycle given Vg = 1.00 kV and is Vout = 12.00 V is D = 0.012 Minimum output voltage Vout_min = 4.81 V

# Imports and setup

from pint import UnitRegistry

# pandas display using scientific notation

# pd.set_option('display.float_format', lambda x: f'{x:.3e}')

# use pint

units = UnitRegistry()
units.default_format = "~P.2f"

In [ ]:
Fs = 10 * units.kilohertz
Ts = 1 / Fs
Tmin_on = 600 * units.nanosecond
Dmin = Tmin_on / Ts
print(f"Minimum duty cycle given Tmin_on = {Tmin_on.to_compact(units.second)} is D

Vg = 1000 * units.volt
Vout = 12 * units.volt
Dwant = Vout / Vg

print(f"Desired duty cycle given Vg = {Vg.to_compact(units.volt)} and is Vout = {Vo

Vdiode = 1 * units.volt
Rds1 = 100 * units.milliohm
RL = 200 * units.milliohm
Iout_min = 1 * units.amp
Vout_min = Tmin_on * Fs * (Vg - (Iout_min * Rds1 - Vdiode)) - (Iout_min * (RL) + Vd # Vout_min = Tmin_on * Fs * Vg

print(f"Minimum output voltage Vout_min = {Vout_min.to_compact(units.volt)}")

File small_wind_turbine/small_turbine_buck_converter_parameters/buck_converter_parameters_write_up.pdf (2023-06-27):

# Buck Converter Design

### Author: Ian Eykamp, Date: June 27, 2023

# Goals

See the notebook of the same name (https://github.com/ianeyk/wind-turbine/blob/main/generic_wind_turbine/initial_buck_converter_parameters/buck_converter_parameters.ipynb) under the folder initial_turbine_buck_converter_parameters for the walkthrough using the original

### numbers and more detailed explanations of what I am doing. This notebook closely mirrors the analysis we followed in Labs 9-11 of Power Electronics. This notebook calculates and then tests the final values used in the buck converter and compensator for the UC2844

feedback loop.

# Import Libraries

The | plecs_helper | library is a file in this directory which has some helper functions for
getting data out of PLECS and for making nice plots.

Using matplotlib backend: TkAgg In [ ]:

import numpy as np
import pandas as pd
import matplotlib.pyplot as plt
import matplotlib.ticker as mtick
from UliEngineering.EngineerIO import format_value from si_prefix import si_format
import plecs_helper as helper
%matplotlib
%matplotlib inline

# Imports and setup

from pint import UnitRegistry

# pandas display using scientific notation

# pd.set_option('display.float_format', lambda x: f'{x:.3e}')

# use pint

units = UnitRegistry()
units.default_format = "~P.2f"

def to_db(gain):
return np.log10(np.abs(gain)) * 20

def to_decibels(gain):
return to_db(gain)

def from_db(db):
return 10 ** (db / 20)

# Schematic

The operation of the buck converter is described elsewhere, not least in the notebook (https://github.com/ianeyk/wind-turbine/blob/main/generic_wind_turbine/initial_buck_converter_parameters/buck_converter_parameters.ipynb) mentioned previously and this detailed design document. (https://docs.google.com/document/d/1PnPaonVPVxOmpUSNjwdRlw55tw-PfFlrPFVEoT9o3yc/edit) This model has a 30V (per phase)

### rectified 3-phase voltage source with 14.5Ω internal resistance, an output capacitance of 200uF, a target output current of 0.25A, and separate current-sensing resistors for the ISENSE pin vs. the compensator. The larger output capacitance significantly reduces the

phase margin on the transfer function, but the compensator still works well, as documented below.

### One other thing to keep in mind is that my feedback loop controls the output current, not

voltage; that is, instead of targeting a certain output voltage like we did in Power Electronics, we are targeting a certain current through the second shunt resistor. How I accomplish this using diff amps is described elsewhere.

### For this model, I also took care to choose inductor and compensator component values that

exist on Digikey. All components are specc'ed in this Google Sheet, (https://docs.google.com/spreadsheets/d/1FKhJxWTBdioV72Y6lbeVeFl75lQ-HYMHbcw-U65tTL4/edit) and the KiCAD schematic is available on my GitHub. (https://github.com/ianeyk/wind-turbine/tree/main/small_wind_turbine/KiCAD/small_wind_turbine) The final PLECS model is here, (https://github.com/ianeyk/wind-turbine/blob/main/small_wind_turbine/3phase_generator_buck_converter.plecs) and the models I used for performing the frequency analyses are in this folder on GitHub. (https://github.com/ianeyk/wind-turbine/tree/main/small_wind_turbine/frequency_analysis_buck_converter)

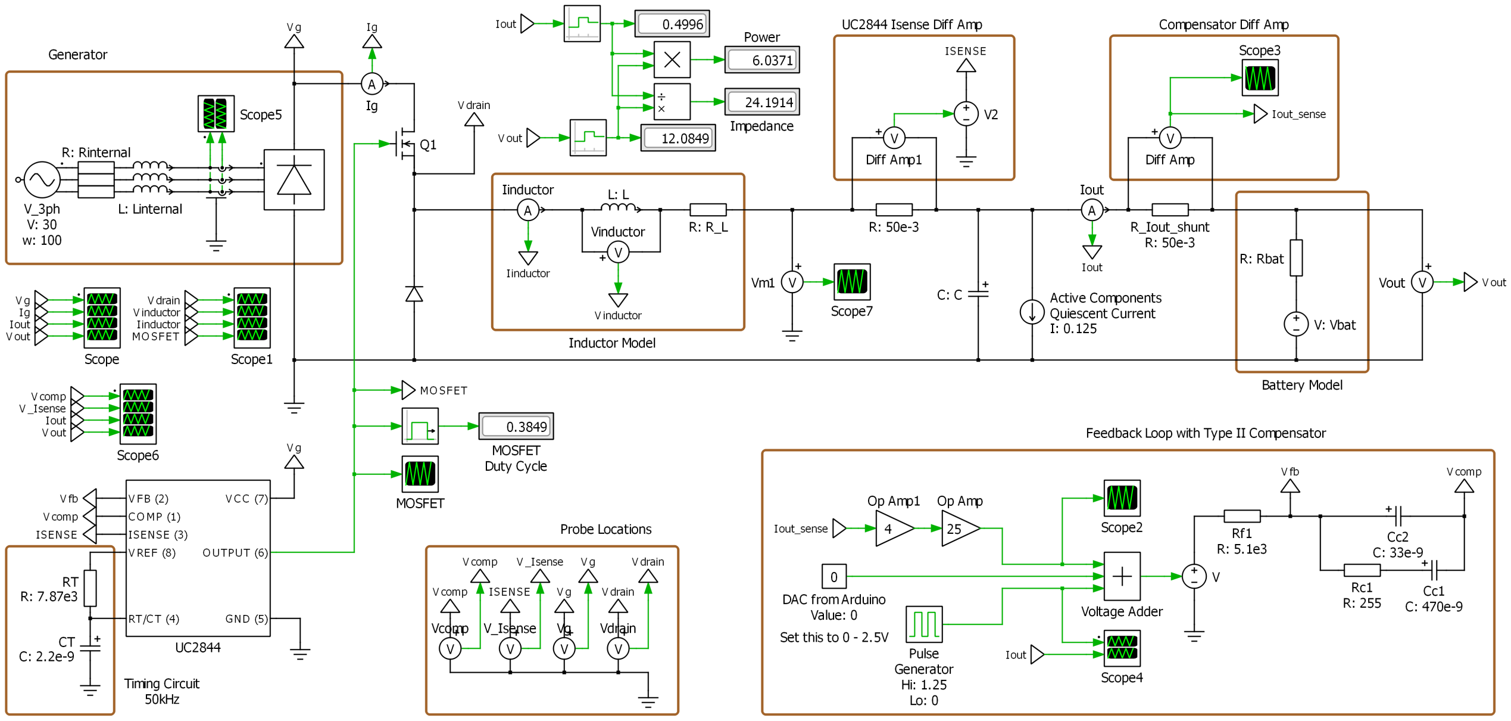
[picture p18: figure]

# Calculate Inductance

### I am nominally aiming for boundary conduction mode (BCM), because this seems like a good balance between limiting the peak inductor voltage and limiting the total energy

stored in the inductor.

In [ ]:

RT = 7.87 * units.kiloohm
CT = 2.2 * units.nanofarad
Fs = 1.72 / (RT * CT) / 2
R_peak_Isense = 50 * units.milliohm

Fs = 49.67 kHz
D = 0.30
L1 (calculated on downward slope) = 338.69 µH
L2 (claculated on upward slope) = 338.69 µH
Vout = 12.04 V
Equivalent impedance = 48.17 Ω, meaning generator output voltage = 39.94 V from 5 1.96 V

### The printouts for L1 and L2 are the same value calculated for the up-going vs. down-going slope of the inductor current. They are expected to be equal for BCM and CCM, which they

are. In reality, I am using a 345uH inductor.

# Plant Frequency Analysis

PLECS Model: frequency_experiment_9a.plecs (https://github.com/ianeyk/wind-turbine/blob/main/small_wind_turbine/frequency_analysis_buck_converter/frequency_experiment_9a.plecs)

R_out_Isense = 100 * units.milliohm
R_L = 200 * units.milliohm # currently unused

Cout = 200 * units.microfarad
# Fs = 50 * units.kilohertz

Ts = 1 / Fs
Ibat = 0.25 * units.amp
Rbat = 0.17 * units.ohm
Vg_nominal = 30 * np.sqrt(3) * units.volt Vbat_nominal = 12 * units.volt Vout_nominal = Vbat_nominal + Ibat * Rbat
R_generator = 14.5 * units.ohm
Z_eq = Vout_nominal / Ibat
Vg_available = Vg_nominal * Z_eq / (R_generator + Z_eq) D_nominal = Vout_nominal / Vg_available
Imin = 0 * units.amp
Ipeak = 2 * Ibat - Imin
L = Vout_nominal * (1 - D_nominal) * Ts / Ipeak
L2 = (Vg_available - Vout_nominal) * D_nominal * Ts / Ipeak

print(f"Fs = {Fs.to_compact(units.hertz)}")
print(f"D = {np.round(D_nominal.to_base_units(), 2)}")
print(f"L1 (calculated on downward slope) = {L.to_compact(units.henry)}") print(f"L2 (claculated on upward slope) = {L2.to_compact(units.henry)}") print(f"Vout = {Vout_nominal.to_compact(units.volt)}")
print(f"Equivalent impedance = {Z_eq.to_compact(units.ohm)}, meaning generator outp

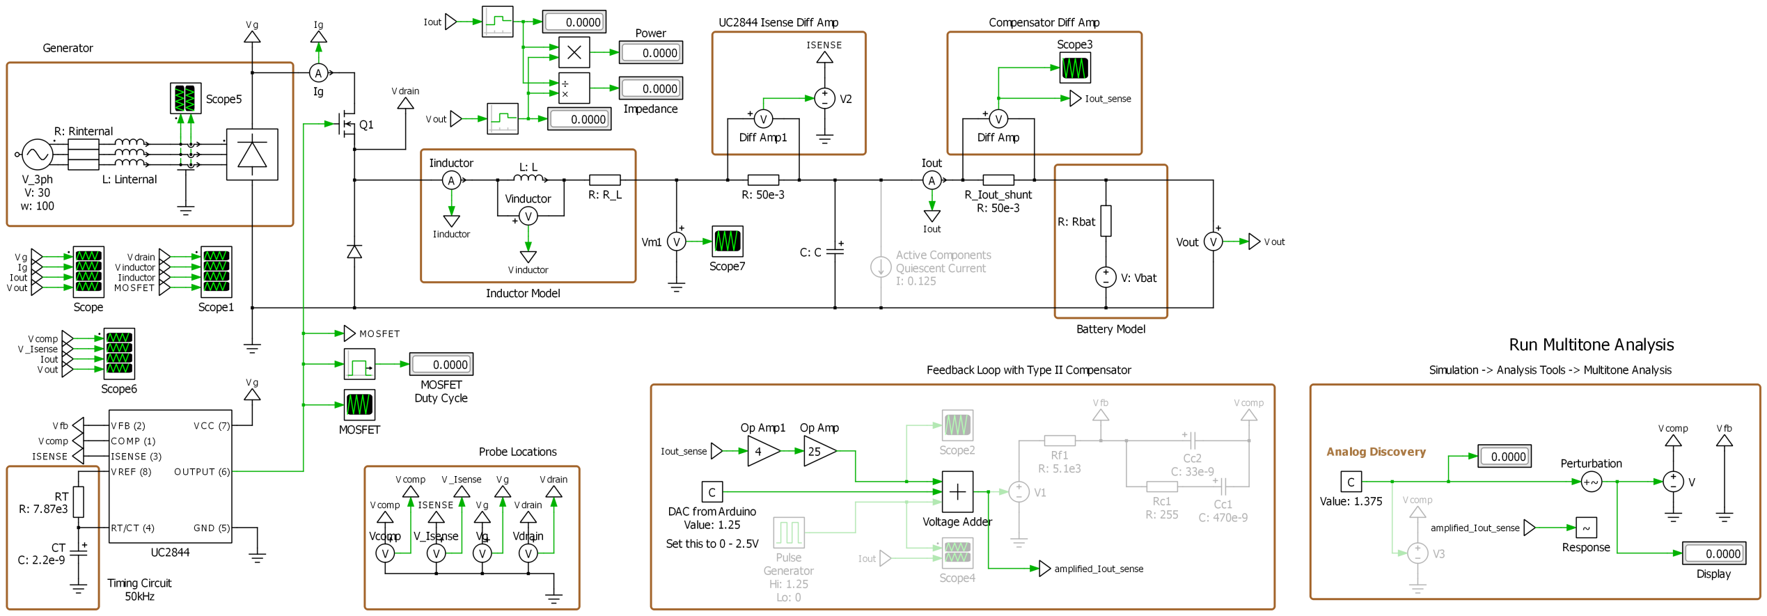
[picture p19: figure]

I plotted the frequency analysis results from my old model. The most relevant difference is

### that the old model had a 100uF capacitor instead of the 200uF in the new model. The new

transfer function is shifted a bit to the left from the old one because of the higher output capacitance.

In [ ]:

df_plant = pd.read_csv("plecs_data/current_500mA/plant_bode_no_quiescent.csv") df_plant.set_axis(["w", "CH1", "CH2"], axis = "columns", inplace = True)

expected_wc = 50e3 / 10
print(f"Lead element center voltage (ω_c): {si_format(expected_wc, precision = 2)}H w = np.logspace(2, 5, 100) # * units.hertz

old_R_Iout_shunt = 5e-3 # * units.ohm
old_Rload = 0.1 # * units.ohm
old_Cload = 200e-6 # * units.farad
old_mystery_factor = 50 # for a total of * 62.5 = 5^4 / 10 = 5^3 / 2 old_theoretical_plant_bode = old_Rload / (1 + (2 * np.pi * 1j * w) * old_Rload * ol

new_R_Iout_shunt = R_peak_Isense.to(units.ohm).magnitude
new_Rload = R_out_Isense.to(units.ohm).magnitude + Rbat.to(units.ohm).magnitude new_Cload = Cout.to(units.farad).magnitude
new_mystery_factor = 31 # 14
theoretical_plant_bode = new_Rload / (1 + (2 * np.pi * 1j * w) * new_Rload * new_Cl

fig, (ax1, ax2) = plt.subplots(nrows = 2, ncols = 1, sharex = False, sharey = False helper.axes_labels("", "Hz", "Gain", "dB", title = "Plant Transfer Function (Magnit ax1.semilogx(w, to_decibels(theoretical_plant_bode), linestyle = "solid", color = " ax1.semilogx(w, to_decibels(old_theoretical_plant_bode), linestyle = "solid", color ax1.semilogx(df_plant["w"], df_plant["CH1"], linestyle = "dotted", color = "green", ax1.axvline(x = expected_wc, linestyle = "dashed", color = "red", label = "Desired ax1.axhline(y = 26, linestyle = "dotted", color = "red", label = "+26dB at desired ax1.axvline(x = 50e3, linestyle = "dashed", color = "black", label = "Switching Fre ax1.legend(loc = "lower left")

helper.axes_labels("Frequency (Hz)", "Hz", "Angle (degrees)", "°", title = "Plant T ax2.semilogx(w, np.angle(theoretical_plant_bode, deg = True), linestyle = "solid", ax2.semilogx(w, np.angle(old_theoretical_plant_bode, deg = True), linestyle = "soli ax2.semilogx(df_plant["w"], df_plant["CH2"], linestyle = "dotted", color = "green", ax2.axvline(x = expected_wc, linestyle = "dashed", color = "red", label = "Desired ax2.axvline(x = 50e3, linestyle = "dashed", color = "black", label = "Switching Fre ax2.legend(loc = "upper left")

Lead element center voltage (ω_c): 5.00 kHz <matplotlib.legend.Legend at 0x2083b9b0400>

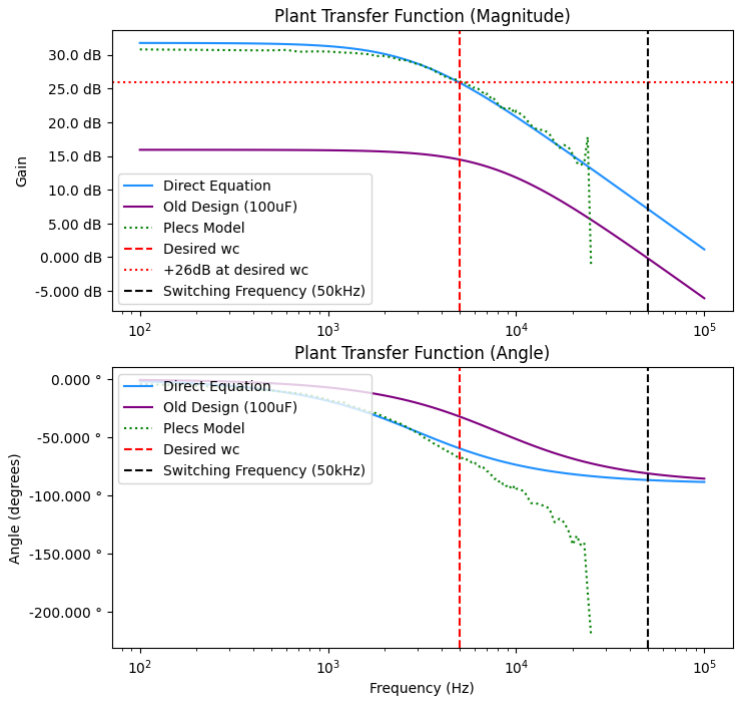
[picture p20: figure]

### Ok, so the PLECS model matches the theory pretty well. I decided on a target crossover

frequency of 5kHz for the current model, instead of 6.25kHz in the previous model. It will respond slightly slower but have a slightly better phase margin. Because of the larger output

### capacitance, the phase margin is way smaller (-60deg vs. -30deg). This can be compensated

for (get it?) with a larger lead element.

# Finding the compensator values

### Using code copied from Lab 11

Design parameters are a gain cross-over frequency at 5kHz, gain factor of -26dB to make the

### gain crossover occur at that frequency (obtained from the simulated transfer function above), and phase boost of 60 degrees. I used a Type II compensator consisting of an

integrating pole and a lead element like we used in class for the buck-boost converter. Out[ ]:

In [ ]:
class Compensator:
def __init__(self, angle_boost_degrees, Kp_decibel_attenuation, Rf1_unitless): self.Rf1 = Rf1_unitless * units.ohm
self.angle_boost = angle_boost_degrees * units.degree
self.Kp = 1 / from_db(Kp_decibel_attenuation)
self.find_values()

def __repr__(self) -> str:
return f"K: {self.K},\t Gc0: {self.Gc0.to_compact()},\t Rf1: {self.Rf1.to_c

def find_values(self):
self.wc = 50 * units.kilohertz * units.revolutions / 10

# self.angle_boost = 60 * units.degree

self.K = np.tan((self.angle_boost / 2 + 45 * units.degree))
# self.Kp = 1 / from_db(26) # from_db(19) # from_db(13) # from_db(32) self.wz = self.wc / self.K

self.wp = self.wc * self.K
self.Gc0 = self.Kp * self.wc * np.sqrt((1 + self.K ** (-2)) / (1 + self.K * self.Cc1 = 1 / (self.Gc0 * self.Rf1)
self.Rc1 = 1 / (self.wz * self.Cc1)
self.Cc2 = 1 / (self.wp * self.Rc1)

for R in [2, 2.2, 2.26, 2.7, 3.3, 3.9, 4.3, 4.7, 4.87, 5.1, 5.6, 6.2, 6.34, 6.8, 7. R_to_highlight = 5.1
if R == R_to_highlight:
print() # highlight the chosen value
compensator = Compensator(angle_boost_degrees = 60, Kp_decibel_attenuation = 26 print(compensator)
if R == R_to_highlight:
print()

K: 3.73, | Gc0: 67.15 Hz·turn, | Rf1: 2.00 kΩ, | Rc1: 100.24 Ω, Cc1: 1.19
µF, | Cc2: 85.09 nF
K: 3.73, | Gc0: 67.15 Hz·turn, | Rf1: 2.20 kΩ, | Rc1: 110.26 Ω, Cc1: 1.08
µF, | Cc2: 77.35 nF
K: 3.73, | Gc0: 67.15 Hz·turn, | Rf1: 2.26 kΩ, | Rc1: 113.27 Ω, Cc1: 1.05
µF, | Cc2: 75.30 nF
K: 3.73, | Gc0: 67.15 Hz·turn, | Rf1: 2.70 kΩ, | Rc1: 135.32 Ω, Cc1: 877.
88 nF, | Cc2: 63.03 nF
K: 3.73, | Gc0: 67.15 Hz·turn, | Rf1: 3.30 kΩ, | Rc1: 165.39 Ω, Cc1: 718.
26 nF, | Cc2: 51.57 nF
K: 3.73, | Gc0: 67.15 Hz·turn, | Rf1: 3.90 kΩ, | Rc1: 195.46 Ω, Cc1: 607.
76 nF, | Cc2: 43.64 nF
K: 3.73, | Gc0: 67.15 Hz·turn, | Rf1: 4.30 kΩ, | Rc1: 215.51 Ω, Cc1: 551.
23 nF, | Cc2: 39.58 nF
K: 3.73, | Gc0: 67.15 Hz·turn, | Rf1: 4.70 kΩ, | Rc1: 235.56 Ω, Cc1: 504.
31 nF, | Cc2: 36.21 nF
K: 3.73, | Gc0: 67.15 Hz·turn, | Rf1: 4.87 kΩ, | Rc1: 244.08 Ω, Cc1: 486.
71 nF, | Cc2: 34.94 nF
K: 3.73, | Gc0: 67.15 Hz·turn, | Rf1: 5.10 kΩ, | Rc1: 255.61 Ω, Cc1: 464.
76 nF, | Cc2: 33.37 nF
K: 3.73, | Gc0: 67.15 Hz·turn, | Rf1: 5.60 kΩ, | Rc1: 280.66 Ω, Cc1: 423.
26 nF, | Cc2: 30.39 nF
K: 3.73, | Gc0: 67.15 Hz·turn, | Rf1: 6.20 kΩ, | Rc1: 310.74 Ω, Cc1: 382.
30 nF, | Cc2: 27.45 nF
K: 3.73, | Gc0: 67.15 Hz·turn, | Rf1: 6.34 kΩ, | Rc1: 317.75 Ω, Cc1: 373.
86 nF, | Cc2: 26.84 nF
K: 3.73, | Gc0: 67.15 Hz·turn, | Rf1: 6.80 kΩ, | Rc1: 340.81 Ω, Cc1: 348.
57 nF, | Cc2: 25.03 nF
K: 3.73, | Gc0: 67.15 Hz·turn, | Rf1: 7.50 kΩ, | Rc1: 375.89 Ω, Cc1: 316.
04 nF, | Cc2: 22.69 nF
K: 3.73, | Gc0: 67.15 Hz·turn, | Rf1: 8.20 kΩ, | Rc1: 410.97 Ω, Cc1: 289.
06 nF, | Cc2: 20.75 nF
K: 3.73, | Gc0: 67.15 Hz·turn, | Rf1: 10.00 kΩ, Rc1: 501.19 Ω, Cc1: 237.
03 nF, | Cc2: 17.02 nF

### The highlighted row yields nice capacitance values fo 33nF and 470nF, which are easily

available. Resistors are chosen at 5.10kΩ and 255Ω, respectively.

# Compensator Transfer Function

PLECS Model: frequency_experiment_compensator_only.plecs (https://github.com/ianeyk/wind-turbine/blob/main/small_wind_turbine/frequency_analysis_buck_converter/frequency_experiment_compensator_only.plecs)

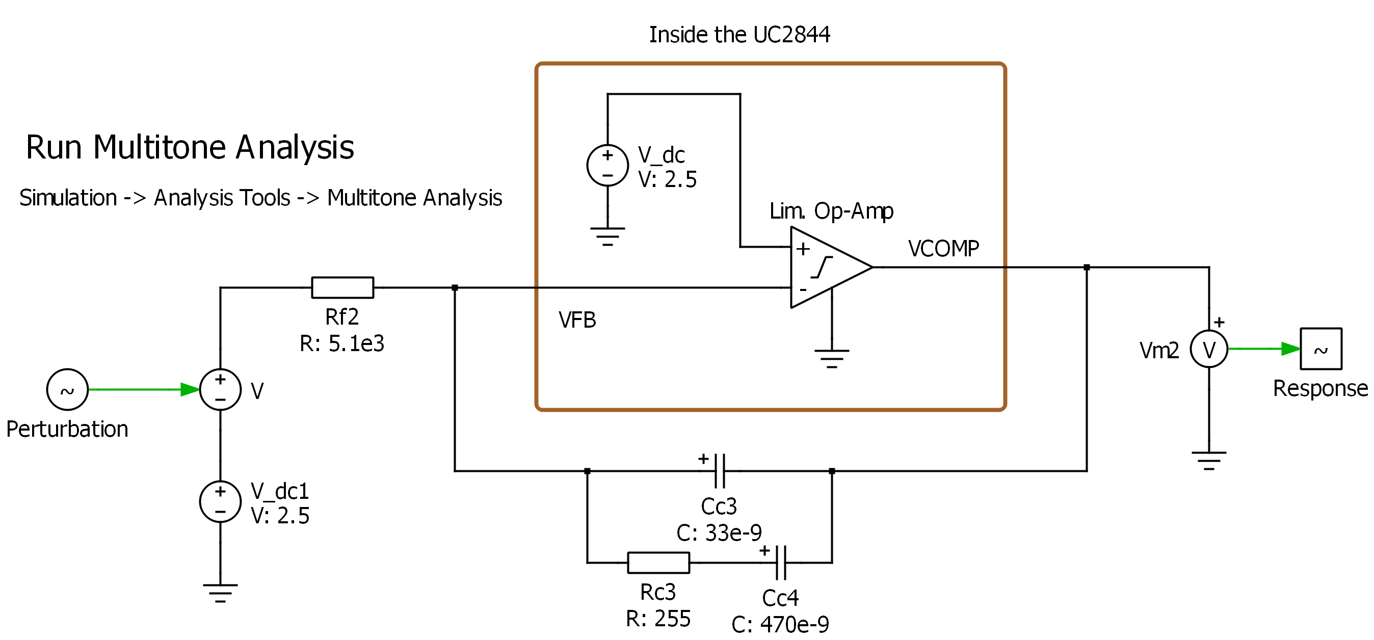
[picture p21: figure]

I ran the frequency analysis in PLECS to determine the transfer function, as well as writing down the equation based on the components. They match exactly.

Lead element center voltage (ω_c): 5.00 kHz In [ ]:

df_compensator = pd.read_csv("plecs_data/current_500mA/compensator_bode.csv") df_compensator.set_axis(["w", "CH1", "CH2"], axis = "columns", inplace = True)

# chosen values

compensator = Compensator(angle_boost_degrees = 60, Kp_decibel_attenuation = 26, Rf Rf1 = compensator.Rf1.to(units.ohm).magnitude
Rc1 = compensator.Rc1.to(units.ohm).magnitude
Cc1 = compensator.Cc1.to(units.farad).magnitude
Cc2 = compensator.Cc2.to(units.farad).magnitude
expected_wc = 1 / (Rc1 * np.sqrt(Cc1 * Cc2)) / 2 / np.pi # to get it into Hz print(f"Lead element center voltage (ω_c): {si_format(expected_wc, precision = 2)}H

w = np.logspace(2, 5, 100) # * units.hertz
def get_Zc(my_w):
my_Zc = 1 / (1 / (Rc1 + 1 / (2 * np.pi * 1j * my_w * Cc1)) + 1 / (1 / (2 * np.p return my_Zc
Zc = get_Zc(w) # direct equation

fig, (ax1, ax2) = plt.subplots(nrows = 2, ncols = 1, sharex = False, sharey = False helper.axes_labels("", "Hz", "Gain", "dB", title = "Zc Gain vs. Frequency (Magnitud ax1.semilogx(w, to_decibels(Zc), linestyle = "solid", color = "dodgerblue", label = ax1.semilogx(df_compensator["w"], df_compensator["CH1"], linestyle = "dotted", colo ax1.axhline(y = -26, linestyle = "dotted", color = "red", label = "-26db Gain at wc ax1.axvline(x = expected_wc, linestyle = "dashed", color = "red", label = "Expected ax1.axvline(x = 50e3, linestyle = "dashed", color = "black", label = "Switching Fre ax1.legend(loc = "lower left")

helper.axes_labels("Frequency (Hz)", "Hz", "Angle (degrees)", "°", title = "Zc Gain ax2.semilogx(w, np.angle(Zc, deg = True), linestyle = "solid", label = "Zc Angle") ax2.semilogx(df_compensator["w"], df_compensator["CH2"] - 180, linestyle = "dotted" ax2.axvline(x = expected_wc, linestyle = "dashed", color = "red", label = "Expected ax2.axvline(x = 50e3, linestyle = "dashed", color = "black", label = "Switching Fre ax2.legend(loc = "upper left")

<matplotlib.legend.Legend at 0x2083be09520>

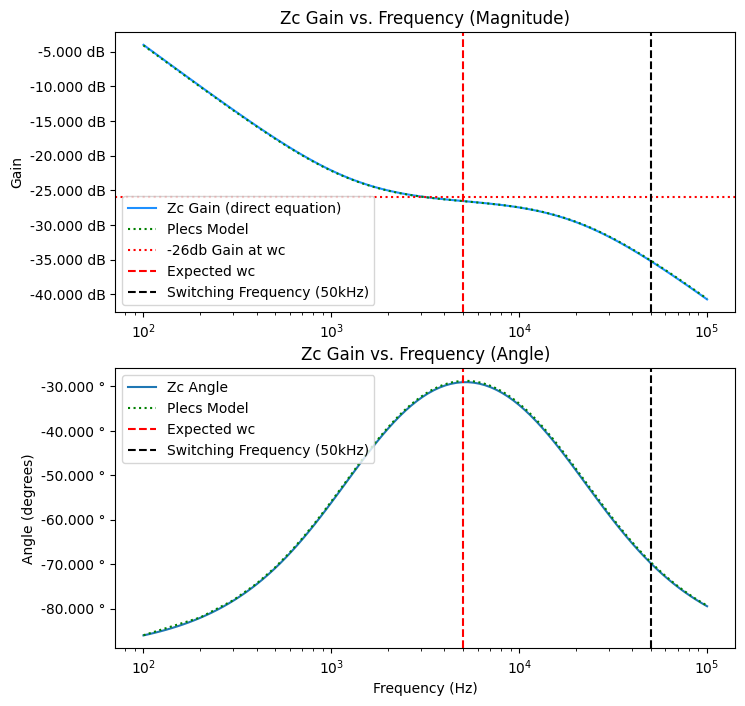
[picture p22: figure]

# Open-Loop Transfer Function

PLECS Model: frequency_experiment_10a.plecs (https://github.com/ianeyk/wind-turbine/blob/main/small_wind_turbine/frequency_analysis_buck_converter/frequency_experiment_10a.plecs)

Out[ ]:

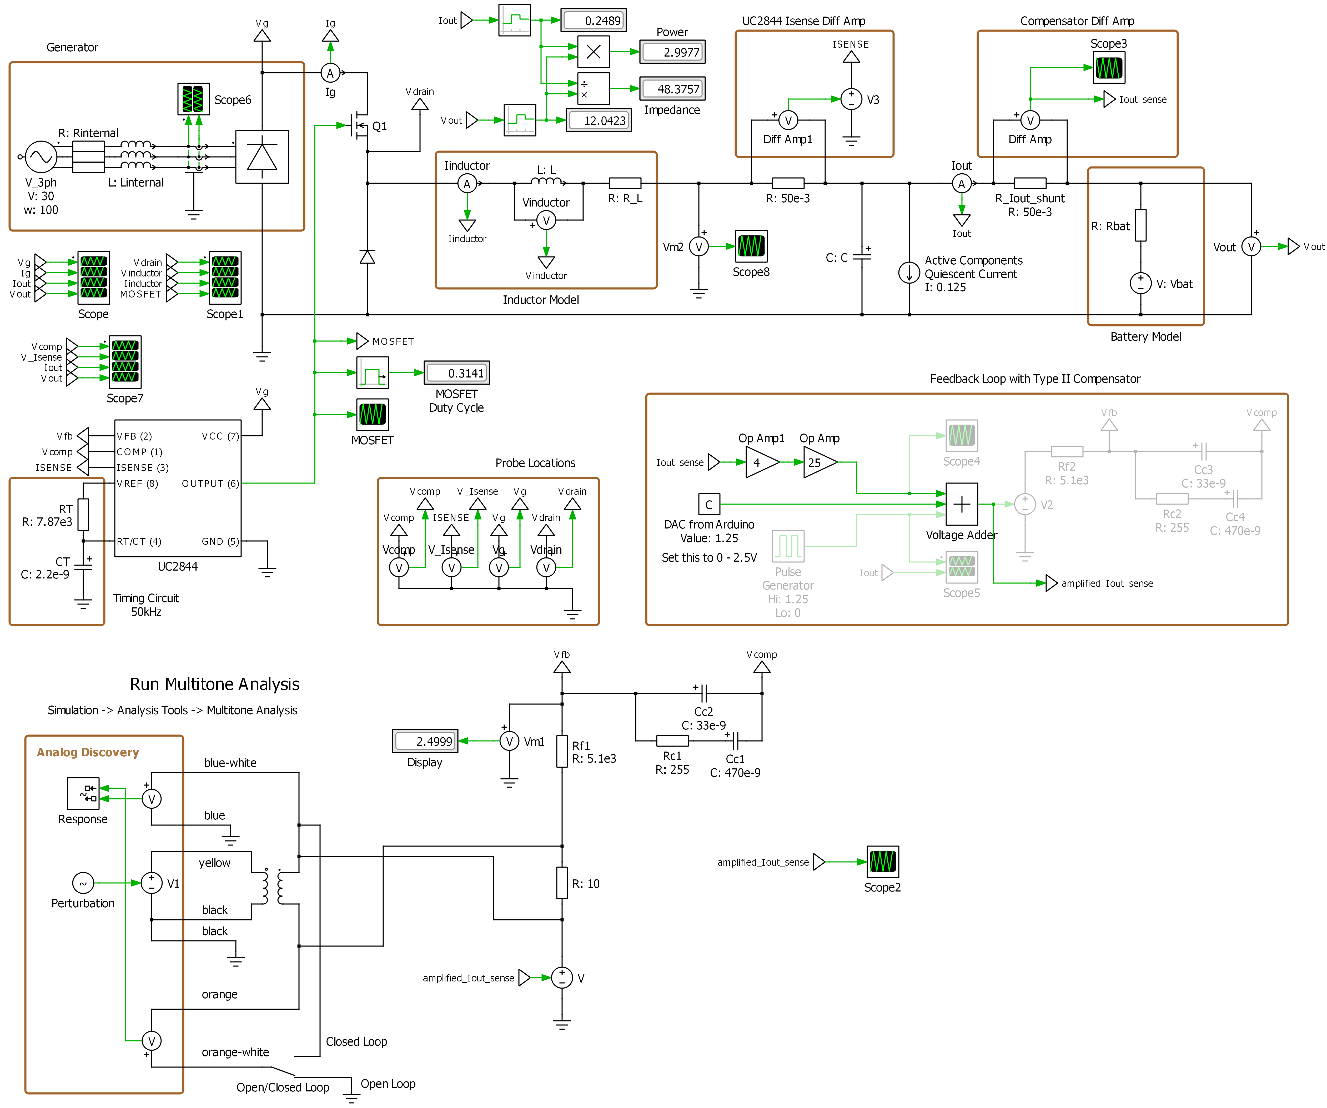
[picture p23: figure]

It looks good! After much debugging of the circuit, I got the transfer function in PLECS to match the expected open-loop transfer function, which is the product of transfer functions for the plant and the compensator. I think my issues were due to trying to use the rightmost shunt resistor for the ISENSE pin on the UC2844, which acted strangely because it is to the right of the capacitor.

### In any case, we have an open-loop transfer function that looks good and matches

expectations. It has infinite gain at DC, a gain crossover frequency at 5kHz as requested, a fat

### phase margin at the crossover frequency, and strong attenuation at high frequencies. The

phase plot falls off a lot faster than expected after the gain crossover frequency, but this is of no real importance to us because the gain margin at the phase crossover frequency is on the order of -15dB.

In [ ]:

# df_open_loop = pd.read_csv("plecs_data/current_500mA/open_loop_bode_no_quiescent. df_open_loop = pd.read_csv("plecs_data/current_500mA/open_loop_bode.csv") df_open_loop.set_axis(["w", "CH1", "CH2"], axis = "columns", inplace = True)

theoretical_open_loop = theoretical_plant_bode * Zc

fig, (ax1, ax2) = plt.subplots(nrows = 2, ncols = 1, sharex = False, sharey = False helper.axes_labels("", "Hz", "Gain", "dB", title = "Open Loop Transfer Function (Ma ax1.semilogx(w, to_decibels(theoretical_open_loop), linestyle = "solid", color = "d ax1.semilogx(df_open_loop["w"], df_open_loop["CH1"], linestyle = "dotted", color =

<matplotlib.legend.Legend at 0x2083c45a8e0>

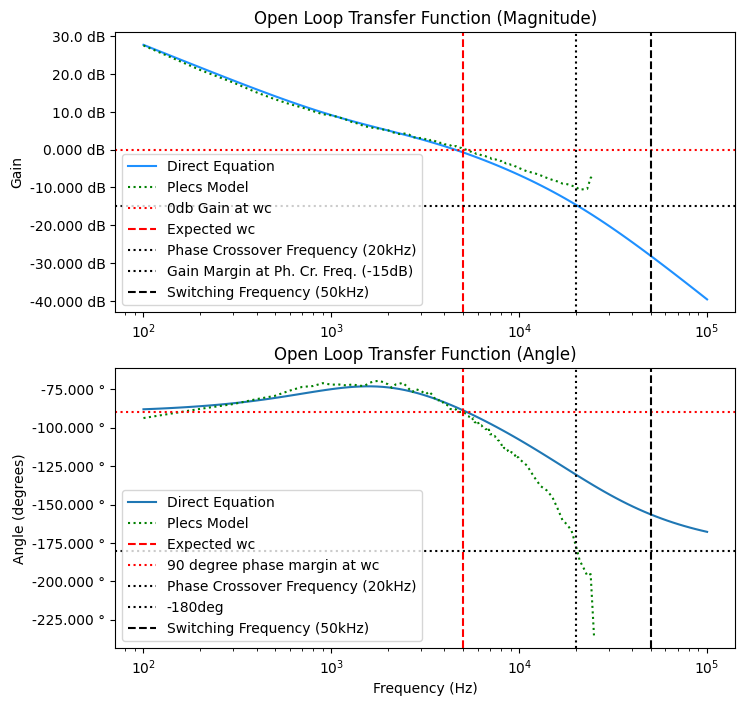
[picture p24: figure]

# Closed-Loop Transfer Function

ax1.axhline(y = 0, linestyle = "dotted", color = "red", label = "0db Gain at wc") ax1.axvline(x = expected_wc, linestyle = "dashed", color = "red", label = "Expected ax1.axvline(x = 20e3, linestyle = "dotted", color = "black", label = "Phase Crossov ax1.axhline(y = -15, linestyle = "dotted", color = "black", label = "Gain Margin at ax1.axvline(x = 50e3, linestyle = "dashed", color = "black", label = "Switching Fre ax1.legend(loc = "lower left")

helper.axes_labels("Frequency (Hz)", "Hz", "Angle (degrees)", "°", title = "Open Lo ax2.semilogx(w, np.angle(theoretical_open_loop, deg = True), linestyle = "solid", l ax2.semilogx(df_open_loop["w"], df_open_loop["CH2"], linestyle = "dotted", color = ax2.axvline(x = expected_wc, linestyle = "dashed", color = "red", label = "Expected ax2.axhline(y = -90, linestyle = "dotted", color = "red", label = "90 degree phase ax2.axvline(x = 20e3, linestyle = "dotted", color = "black", label = "Phase Crossov ax2.axhline(y = -180, linestyle = "dotted", color = "black", label = "-180deg") ax2.axvline(x = 50e3, linestyle = "dashed", color = "black", label = "Switching Fre ax2.legend(loc = "lower left")

Out[ ]:

PLECS Model: Same as open-loop | frequency_experiment_10a.plecs (https://github.com/ianeyk/wind-turbine/blob/main/small_wind_turbine/frequency_analysis_buck_converter/frequency_experiment_10a.plecs) | except flip the
switch from the open-loop side to the closed-loop side on the Analog Discovery model.


<matplotlib.legend.Legend at 0x20836963d60> In [ ]:

df_closed_loop = pd.read_csv("plecs_data/current_500mA/closed_loop_bode_no_quiescen # df_closed_loop = pd.read_csv("plecs_data/current_500mA/closed_loop_bode.csv") df_closed_loop.set_axis(["w", "CH1", "CH2"], axis = "columns", inplace = True)

theoretical_closed_loop = theoretical_open_loop / (1 + theoretical_open_loop)

fig, (ax1, ax2) = plt.subplots(nrows = 2, ncols = 1, sharex = False, sharey = False helper.axes_labels("", "Hz", "Gain", "dB", title = "Closed Loop Transfer Function ( ax1.semilogx(w, to_decibels(theoretical_closed_loop), linestyle = "solid", color = ax1.semilogx(df_closed_loop["w"], df_closed_loop["CH1"], linestyle = "dotted", colo ax1.axvline(x = expected_wc, linestyle = "dashed", color = "red", label = "Expected ax1.axvline(x = 50e3, linestyle = "dashed", color = "black", label = "Switching Fre ax1.legend(loc = "lower left")

helper.axes_labels("Frequency (Hz)", "Hz", "Angle (degrees)", "°", title = "Closed ax2.semilogx(w, np.angle(theoretical_closed_loop, deg = True), linestyle = "solid", ax2.semilogx(df_closed_loop["w"], df_closed_loop["CH2"], linestyle = "dotted", colo ax2.axvline(x = expected_wc, linestyle = "dashed", color = "red", label = "Expected ax2.axvline(x = 50e3, linestyle = "dashed", color = "black", label = "Switching Fre ax2.legend(loc = "upper left")

Out[ ]:


### Again, the theory and the PLECS model match pretty well. The system has a gain of 1 at DC

and strong attenuation well before the switching frequency, exactly as we want.

# Time Response

Lastly, I implemented a square wave signal to the voltage adder to simulate a change in the desired current. The PLECS model (https://github.com/ianeyk/wind-turbine/blob/main/small_wind_turbine/3phase_generator_buck_converter.plecs) is the same model shown at the start of this notebook.


<matplotlib.legend.Legend at 0x2083c50a2b0>

In [ ]:

df = pd.read_csv("plecs_data/current_500mA/square_wave_response_lower_current.csv") df.rename(mapper = helper.strip_labels, axis = "columns", inplace = True) df["Iexpected"] = .5 * (1 - df["Pulse Generator"] / 2.5) - 0.25
df_zoom = df.loc[(df["Time / s"] > 10e-3) & (df["Time / s"] < 40e-3)]

fig, (ax1) = plt.subplots(nrows = 1, ncols = 1, sharex = True, sharey = False, figs # ax2 = ax1.twinx()
fig.autofmt_xdate()
ax1.plot(df_zoom["Time / s"], df_zoom["Iout"], color = "orange", label = "Iout") ax1.plot(df_zoom["Time / s"], df_zoom["Iexpected"], color = "blue", label = "Desire helper.axes_labels("Simulation time", "s", "Current", "A", title = "Step Response", ax1.legend(loc = "upper right")

df_zoom = df.loc[(df["Time / s"] > 24.8e-3) & (df["Time / s"] < 25.8e-3)]

fig, (ax1) = plt.subplots(nrows = 1, ncols = 1, sharex = True, sharey = False, figs # ax2 = ax1.twinx()
fig.autofmt_xdate()
helper.axes_labels("Simulation time", "s", "Current", "A", title = "Step Response ( ax1.plot(df_zoom["Time / s"], df_zoom["Iout"], color = "orange", label = "Iout") ax1.plot(df_zoom["Time / s"], df_zoom["Iexpected"], color = "blue", label = "Desire ax1.legend(loc = "upper right")

Out[ ]:


The output current adjusts to the specified value within about half a millisecond, which is fast enough for my application.

The 200uF output capacitor keeps the small-scale current ripple within about 40mA peak-to-peak, which is highly desirable. In the top graph, you can also see some ripple on the 2ms

### time scale. This corresponds to peaks and troughs in the input voltage due to the 3-phase

AC voltage source and subsequent rectification. It is small enough to be very manageable.

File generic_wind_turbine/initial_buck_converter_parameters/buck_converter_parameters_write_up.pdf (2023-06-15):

# Buck Converter Design

### Author: Ian Eykamp, Date: June 15, 2023

# Goals

### To design a buck converter which can take in a large range of input voltages and output a

controllable current to a battery. It should be robust to different input voltages and different battery models.

### I chose some made-up parameters which I will replace once I am ready to design the real

PCB. For example, I gave the battery a nominal voltage of 12V with a 0.1Ω internal resistance. This will be updated once I do some testing / read the datasheet on the batteries. Also, I did

### not worry about choosing resistor and capacitor values which exist in real life. This simulation is just to prove the concept that I can create a buck converter with a working

control loop.

Using matplotlib backend: TkAgg

In [ ]:

import numpy as np
import pandas as pd
import matplotlib.pyplot as plt
import matplotlib.ticker as mtick
from UliEngineering.EngineerIO import format_value from si_prefix import si_format
import plecs_helper as helper
%matplotlib
%matplotlib inline

# Imports and setup

from pint import UnitRegistry

# pandas display using scientific notation

# pd.set_option('display.float_format', lambda x: f'{x:.3e}')

# use pint

units = UnitRegistry()
units.default_format = "~P.2f"

def to_db(gain):
return np.log10(np.abs(gain)) * 20

def to_decibels(gain):
return to_db(gain)

def from_db(db):
return 10 ** (db / 20)

# Schematic

### The buck converter follows the one we developed in class. The new features are a battery model in place of a load resistor and a current-sensing control loop instead of an output

voltage control loop.

The battery model consists of a 12V nominal voltage source in series with a 0.1Ω resistor. This is based on what Beat told me to do. I might be able to replace it with a more accurate battery model, but I do not know if I need to. At least, I will perform measurements or read the datasheet to find the parameters of the real battery I will be using.

The current control loop consists of a shunt resistor in series with the battery straddled by a differential amplifier. The diff amp acts like a voltmeter since it finds the voltage drop across the resistor. I want a nominal 20A charging rate, so I chose a shunt resistance value of 5mΩ. That means a 20A current will create a 0.1V drop across the shunt resistor. The diff amp's value is fed into an op-amp configured as a non-inverting amplifier with a gain of 25. Thus the 0.1V drop will become a 2.5V signal. This is the signal that is fed into the UC2844 and the compensator.

### There is one more step, which is a voltage adder connected to an analog pin coming from an Arduino. This voltage is added to the amplified current-sensing signal, such that the

output will reach 2.5V at a lower voltage. It turns out that the control loop obeys this voltage
adder and works to make the output current equal to | , where | is

### the analog voltage created by the Arduino. I am probably going to implement this voltage

adder using the same op amp as I will use for the gain.


# Define measured constants and nominal values

20A ⋅ (1 − | )

Vcontrol
2.5V | Vcontrol

### I aimed for nominally operating very close to boundary condition mode (BCM), but slightly

in CCM. Since it is operating with a large amount of current, I thought it was a good balance

### between energy stored in the inductor and allowing current to flow continuously into the

battery (reducing ripple).

D = 0.40
L = 5.33 µH
Vout = 16.00 V

# Plant Frequency Analysis

### Ok, so here's where I took a shortcut. Before doing any frequency analysis or compensator design in class, we went through a whole derivation of the large-signal and small-signal models for the buck-boost converter and came up with a theoretical prediction of what the

plant transfer function would look like. I tried to comprehend the latter half of Chapter 12 in Fundamentals of Power Electronics, but I got lost in all the math and could not reproduce this derivation for the buck converter. I found Table 12.3 in that textbook which listed the simple
model transfer function as being | , where | is presumably the transfer

### function I am looking for and is the load resistance and is the load capacitance. Simple

enough! I hope it's right.

With that in hand, I went into PLECS and made a bode plot of the plant transfer function just like we did with the physical hardware in Lab 9. Below, I plotted the simulated results of the multitone analysis. Apart from a relatively large constant offset, it matches the textbook equation pretty well.

In [ ]:
Cout = 100 * units.microfarad Fs = 50 * units.kilohertz
Ts = 1 / Fs
Ibat = 20 * units.amp
Rbat = 0.1 * units.ohm
Vg_nominal = 40 * units.volt
Vbat_nominal = 12 * units.volt + Ibat * Rbat Rbat = 0.1 * units.ohm
Vout_nominal = Vbat_nominal + Ibat * Rbat
D_nominal = Vout_nominal / Vg_nominal
Imin = 2 * units.amp
L = Vout_nominal / (2 * (Ibat - Imin)) * (1 - D_nominal) * Ts

print(f"D = {np.round(D_nominal, 2)}")
print(f"L = {L.to_compact(units.henry)}")
print(f"Vout = {Vout_nominal.to_compact(units.volt)}")

=

v^

^ic

R
1+sRC

?= Gp
v^

^ic
R | C


Lead element center voltage (ω_c): 6.25 kHz <matplotlib.legend.Legend at 0x1f226a04c10>

In [ ]:

df_plant = pd.read_csv("plecs_data/plant_bode.csv")
df_plant.set_axis(["w", "CH1", "CH2"], axis = "columns", inplace = True)

expected_wc = 50e3 / 8 # to get it into Hz
print(f"Lead element center voltage (ω_c): {si_format(expected_wc, precision = 2)}H w = np.logspace(2, 5, 100) # * units.hertz

R_Iout_shunt = 5e-3 # * units.ohm
Rload = 0.1 # * units.ohm
Cload = 200e-6 # * units.farad
mystery_factor = 50 # for a total of * 62.5 = 5^4 / 10 = 5^3 / 2 theoretical_plant_bode = Rload / (1 + (2 * np.pi * 1j * w) * Rload * Cload) / Rload

fig, (ax1, ax2) = plt.subplots(nrows = 2, ncols = 1, sharex = False, sharey = False helper.axes_labels("", "Hz", "Gain", "dB", title = "Plant Transfer Function (Magnit ax1.semilogx(w, to_decibels(theoretical_plant_bode), linestyle = "solid", color = " ax1.semilogx(df_plant["w"], df_plant["CH1"], linestyle = "dotted", color = "green", ax1.axvline(x = expected_wc, linestyle = "dashed", color = "red", label = "Desired ax1.axvline(x = 50e3, linestyle = "dashed", color = "black", label = "Switching Fre ax1.legend(loc = "lower left")

helper.axes_labels("Frequency (Hz)", "Hz", "Angle (degrees)", "°", title = "Plant T ax2.semilogx(w, np.angle(theoretical_plant_bode, deg = True), linestyle = "solid", ax2.semilogx(df_plant["w"], df_plant["CH2"], linestyle = "dotted", color = "green", ax2.axvline(x = expected_wc, linestyle = "dashed", color = "red", label = "Desired ax2.axvline(x = 50e3, linestyle = "dashed", color = "black", label = "Switching Fre ax2.legend(loc = "upper left")

Out[ ]:


### Ok, so the PLECS model matches the theory pretty well. You will notice that the magnitude

plot matches almost exactly, but I said they were off by a significant factor. What I've shown in the graph above is after multiplying the theoretical curve by a magical factor of 50 to make them line up.

mystery_factor = 50
theoretical_plant_bode = Rload / (1 + (2 * np.pi * 1j * w) * Rload
* Cload) / Rload * R_Iout_shunt * 25 * mystery_factor
More clarification on the above line of code: | Rload / (1 + (2 * np.pi * 1j * w) *
Rload * Cload) | This is the equation given in the textbook as | , with some terms to
convert from real-valued | w | in Hertz to complex-valued in radians per second. But this
equation is designed to capture the transfer function from | to | , and I want from
to | . To convert | into | , I use | / Rload | to convert output voltage into to

### current (assuming the equation was designed for a regular load resistor, not a battery

model), | * R_Iout_shunt | to convert the current into the voltage seen by the diff amp, and
* 25 | for the amplifier. There is still a mystery factor of | * mystery_factor | , which I

R
1+sRC
s
Ipeak | Vout
VCOMP | VFB | Vout | VFB

assume originates from the conversion of | through the innards of the UC2844 and
into | .

### There is obviously some second order behaviour going on above a couple of kHz, especially

for the angle, but I'm hoping I can just ignore that.

# Finding the compensator values

### Using code copied from Lab 11

Design parameters are a gain cross-over frequency at 6.25kHz, gain factor of -13dB to make

### the gain crossover occur at that frequency (obtained from the simulated transfer function above), and phase boost of 30 degrees. I used a Type II compensator consisting of an

integrating pole and a lead element like we used in class for the buck-boost converter.

VCOMP

Ipeak

In [ ]:

class Compensator:
def __init__(self, Rf1_unitless): self.Rf1 = Rf1_unitless * units.ohm
self.find_values()

def __repr__(self) -> str:
return f"K: {self.K},\t Gc0: {self.Gc0.to_compact()},\t Rf1: {self.Rf1.to_c

def find_values(self):
self.wc = 50 * units.kilohertz * units.revolutions / 8

self.angle_boost = 30 * units.degree
self.K = np.tan((self.angle_boost / 2 + 45 * units.degree)) self.Kp = 1 / from_db(13) # from_db(32)
self.wz = self.wc / self.K
self.wp = self.wc * self.K
self.Gc0 = self.Kp * self.wc * np.sqrt((1 + self.K ** (-2)) / (1 + self.K * self.Cc1 = 1 / (self.Gc0 * self.Rf1)
self.Rc1 = 1 / (self.wz * self.Cc1)
self.Cc2 = 1 / (self.wp * self.Rc1)

for R in [2, 2.2, 2.7, 3.3, 3.9, 4.3, 4.7, 5.1, 5.6, 6.2, 6.8, 7.5, 8.2, 10]: # val R_to_highlight = 5.6
if R == R_to_highlight:
print() # highlight the chosen value compensator = Compensator(R * 1e3) print(compensator)
if R == R_to_highlight:
print()

K: 1.73, | Gc0: 807.83 Hz·turn, | Rf1: 2.00 kΩ, | Rc1: 447.74 Ω, Cc1: 98.5
1 nF, | Cc2: 32.84 nF
K: 1.73, | Gc0: 807.83 Hz·turn, | Rf1: 2.20 kΩ, | Rc1: 492.52 Ω, Cc1: 89.5
5 nF, | Cc2: 29.85 nF
K: 1.73, | Gc0: 807.83 Hz·turn, | Rf1: 2.70 kΩ, | Rc1: 604.45 Ω, Cc1: 72.9
7 nF, | Cc2: 24.32 nF
K: 1.73, | Gc0: 807.83 Hz·turn, | Rf1: 3.30 kΩ, | Rc1: 738.78 Ω, Cc1: 59.7
0 nF, | Cc2: 19.90 nF
K: 1.73, | Gc0: 807.83 Hz·turn, | Rf1: 3.90 kΩ, | Rc1: 873.10 Ω, Cc1: 50.5
2 nF, | Cc2: 16.84 nF
K: 1.73, | Gc0: 807.83 Hz·turn, | Rf1: 4.30 kΩ, | Rc1: 962.65 Ω, Cc1: 45.8
2 nF, | Cc2: 15.27 nF
K: 1.73, | Gc0: 807.83 Hz·turn, | Rf1: 4.70 kΩ, | Rc1: 1.05 kΩ, | Cc1: 41.9
2 nF, | Cc2: 13.97 nF
K: 1.73, | Gc0: 807.83 Hz·turn, | Rf1: 5.10 kΩ, | Rc1: 1.14 kΩ, | Cc1: 38.6
3 nF, | Cc2: 12.88 nF
K: 1.73, | Gc0: 807.83 Hz·turn, | Rf1: 5.60 kΩ, | Rc1: 1.25 kΩ, | Cc1: 35.1
8 nF, | Cc2: 11.73 nF
K: 1.73, | Gc0: 807.83 Hz·turn, | Rf1: 6.20 kΩ, | Rc1: 1.39 kΩ, | Cc1: 31.7
8 nF, | Cc2: 10.59 nF
K: 1.73, | Gc0: 807.83 Hz·turn, | Rf1: 6.80 kΩ, | Rc1: 1.52 kΩ, | Cc1: 28.9
7 nF, | Cc2: 9.66 nF
K: 1.73, | Gc0: 807.83 Hz·turn, | Rf1: 7.50 kΩ, | Rc1: 1.68 kΩ, | Cc1: 26.2
7 nF, | Cc2: 8.76 nF
K: 1.73, | Gc0: 807.83 Hz·turn, | Rf1: 8.20 kΩ, | Rc1: 1.84 kΩ, | Cc1: 24.0
3 nF, | Cc2: 8.01 nF
K: 1.73, | Gc0: 807.83 Hz·turn, | Rf1: 10.00 kΩ, Rc1: 2.24 kΩ, | Cc1: 19.7
0 nF, | Cc2: 6.57 nF

# Compensator Transfer Function

The values I chose for the compensator are shown in the schematic below. These will change

### when I update the model parameters for my final design, but the behavior of the

compensator should remain the same.


I ran the frequency analysis in PLECS to determine the transfer function, as well as writing down the equation based on the components. They match exactly.

In [ ]:
df_compensator = pd.read_csv("plecs_data/compensator_bode.csv") df_compensator.set_axis(["w", "CH1", "CH2"], axis = "columns", inplace = True)

# chosen values

compensator = Compensator(5.6 * 1e3)
Rf1 = compensator.Rf1.to(units.ohm).magnitude
Rc1 = compensator.Rc1.to(units.ohm).magnitude
Cc1 = compensator.Cc1.to(units.farad).magnitude
Cc2 = compensator.Cc2.to(units.farad).magnitude
expected_wc = 1 / (Rc1 * np.sqrt(Cc1 * Cc2)) / 2 / np.pi # to get it into Hz print(f"Lead element center voltage (ω_c): {si_format(expected_wc, precision = 2)}H

w = np.logspace(2, 5, 100) # * units.hertz
def get_Zc(my_w):
my_Zc = 1 / (1 / (Rc1 + 1 / (2 * np.pi * 1j * my_w * Cc1)) + 1 / (1 / (2 * np.p return my_Zc
Zc = get_Zc(w) # direct equation

fig, (ax1, ax2) = plt.subplots(nrows = 2, ncols = 1, sharex = False, sharey = False helper.axes_labels("", "Hz", "Gain", "dB", title = "Zc Gain vs. Frequency (Magnitud ax1.semilogx(w, to_decibels(Zc), linestyle = "solid", color = "dodgerblue", label = ax1.semilogx(df_compensator["w"], df_compensator["CH1"], linestyle = "dotted", colo ax1.axhline(y = -15, linestyle = "dotted", color = "red", label = "-15db Gain at wc ax1.axvline(x = expected_wc, linestyle = "dashed", color = "red", label = "Expected ax1.axvline(x = 50e3, linestyle = "dashed", color = "black", label = "Switching Fre ax1.legend(loc = "lower left")

Lead element center voltage (ω_c): 6.25 kHz <matplotlib.legend.Legend at 0x1f226b29d00>


# Open-Loop Transfer Function

helper.axes_labels("Frequency (Hz)", "Hz", "Angle (degrees)", "°", title = "Zc Gain ax2.semilogx(w, np.angle(Zc, deg = True), linestyle = "solid", label = "Zc Angle") ax2.semilogx(df_compensator["w"], df_compensator["CH2"] + 180, linestyle = "dotted" ax2.axvline(x = expected_wc, linestyle = "dashed", color = "red", label = "Expected ax2.axvline(x = 50e3, linestyle = "dashed", color = "black", label = "Switching Fre ax2.legend(loc = "upper left")

Out[ ]:


### I implemented the compensator in PLECS and ran open-loop and closed-loop frequency

analyses, copying the Analog Discovery (AD2) model from Lab 10. Lo and behold, it does the

### things we want, including infinite open-loop gain at DC, a crossover frequency where we wanted it, and an excellent phase margin between 70 and 90 degrees, depending on if

you're looking at the PLECS results or the theoretical equation.

In [ ]:

df_open_loop = pd.read_csv("plecs_data/open_loop_bode.csv") df_open_loop.set_axis(["w", "CH1", "CH2"], axis = "columns", inplace = True)

theoretical_open_loop = theoretical_plant_bode * Zc

fig, (ax1, ax2) = plt.subplots(nrows = 2, ncols = 1, sharex = False, sharey = False helper.axes_labels("", "Hz", "Gain", "dB", title = "Open Loop Transfer Function (Ma ax1.semilogx(w, to_decibels(theoretical_open_loop), linestyle = "solid", color = "d ax1.semilogx(df_open_loop["w"], df_open_loop["CH1"], linestyle = "dotted", color = ax1.axhline(y = 0, linestyle = "dotted", color = "red", label = "0db Gain at wc") ax1.axvline(x = expected_wc, linestyle = "dashed", color = "red", label = "Expected ax1.axvline(x = 50e3, linestyle = "dashed", color = "black", label = "Switching Fre ax1.legend(loc = "lower left")

helper.axes_labels("Frequency (Hz)", "Hz", "Angle (degrees)", "°", title = "Open Lo ax2.semilogx(w, np.angle(theoretical_open_loop, deg = True), linestyle = "solid", l ax2.semilogx(df_open_loop["w"], df_open_loop["CH2"], linestyle = "dotted", color = ax2.axvline(x = expected_wc, linestyle = "dashed", color = "red", label = "Expected ax2.axvline(x = 50e3, linestyle = "dashed", color = "black", label = "Switching Fre ax2.legend(loc = "upper left")

<matplotlib.legend.Legend at 0x1f226f61a30>


# Closed-Loop Transfer Function

Out[ ]:


<matplotlib.legend.Legend at 0x1f2285b95b0>

In [ ]:

df_closed_loop = pd.read_csv("plecs_data/closed_loop_bode.csv") df_closed_loop.set_axis(["w", "CH1", "CH2"], axis = "columns", inplace = True)

theoretical_closed_loop = theoretical_open_loop / (1 + theoretical_open_loop)

fig, (ax1, ax2) = plt.subplots(nrows = 2, ncols = 1, sharex = False, sharey = False helper.axes_labels("", "Hz", "Gain", "dB", title = "Closed Loop Transfer Function ( ax1.semilogx(w, to_decibels(theoretical_closed_loop), linestyle = "solid", color = ax1.semilogx(df_closed_loop["w"], df_closed_loop["CH1"], linestyle = "dotted", colo ax1.axvline(x = expected_wc, linestyle = "dashed", color = "red", label = "Expected ax1.axvline(x = 50e3, linestyle = "dashed", color = "black", label = "Switching Fre ax1.legend(loc = "lower left")

helper.axes_labels("Frequency (Hz)", "Hz", "Angle (degrees)", "°", title = "Closed ax2.semilogx(w, np.angle(theoretical_closed_loop, deg = True), linestyle = "solid", ax2.semilogx(df_closed_loop["w"], df_closed_loop["CH2"], linestyle = "dotted", colo ax2.axvline(x = expected_wc, linestyle = "dashed", color = "red", label = "Expected ax2.axvline(x = 50e3, linestyle = "dashed", color = "black", label = "Switching Fre ax2.legend(loc = "upper left")

Out[ ]:


### Again, the theory and the PLECS model match pretty well. The system has a gain of 1 at DC

and strong attenuation well before the switching frequency, exactly as we want.

# Time Response

Lastly, I implemented a square wave signal to the voltage adder to simulate a change in the desired current.


<matplotlib.legend.Legend at 0x1f225a7feb0>


There is significant ripple in the output current, but the average value approaches the set point very quickly. The system appears slightly underdamped, since there is no overshoot, but it still settles within a quarter of a millisecond, which is fast enough for me. The ripple can be significantly reduced by increasing the load capacitance, say from 100uF to 200uF, although this would likely change the plant transfer function and necessitate recalculating the compensator values.

In [ ]:

df = pd.read_csv("plecs_data/square_wave_response.csv")
df.rename(mapper = helper.strip_labels, axis = "columns", inplace = True) df["Iexpected"] = 20 * (1 - df["Pulse Generator"] / 2.5)
df_zoom = df.loc[(df["Time / s"] > 6e-3) & (df["Time / s"] < 8e-3)]

fig, (ax1) = plt.subplots(nrows = 1, ncols = 1, sharex = True, sharey = False, figs # ax2 = ax1.twinx()
fig.autofmt_xdate()
ax1.plot(df_zoom["Time / s"], df_zoom["Iexpected"], color = "blue", label = "Desire ax1.plot(df_zoom["Time / s"], df_zoom["Iout"], color = "orange", label = "Iout") helper.axes_labels("Simulation time", "s", "Current", "A", title = "UC28844 Normal ax1.legend(loc = "upper right")

Out[ ]:

# Next Steps

If this design looks good to you, I will start refining the parameter values, such as the input voltage, desired current, and battery model. With the updated parameters, I will re-run the simulation and make sure it behaves as I expect. Then I will probably start speccing physical components and designing a PCB in KiCAD.

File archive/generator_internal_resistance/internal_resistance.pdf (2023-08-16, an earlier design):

# Generator Internal Resistance Calculations

### Author: Ian Eykamp, Date: 6/16/2023

# Purpose

All generators have some amount of internal resistance, which allows there to be a variable

### voltage drop across the terminals, even if the generator always outputs the same emf. By

connecting various resistors across the terminals (using no resistance as a baseline), I can figure out what the internal resistance is.

# Import libraries

plecs_helper.py is a file I created which defines some helper functions for nice plots and getting data off the oscilloscope and out of PLECS.

Using matplotlib backend: <object object at 0x0000029CAE9AC580> C:\Users\ieykamp\AppData\Local\Packages\PythonSoftwareFoundation.Python.3.9_qbz5n2 kfra8p0\LocalCache\local-packages\Python39\site-packages\scipy\__init__.py:146: Us erWarning: A NumPy version >=1.16.5 and <1.23.0 is required for this version of Sc iPy (detected version 1.23.1

warnings.warn(f"A NumPy version >={np_minversion} and <{np_maxversion}" In [ ]: import numpy as np
import pandas as pd
import matplotlib.pyplot as plt
import matplotlib.ticker as mtick
from UliEngineering.EngineerIO import format_value from si_prefix import si_format
import plecs_helper as helper
%matplotlib
%matplotlib inline

# Imports and setup

from pint import UnitRegistry, Quantity from scipy.signal import find_peaks
from scipy.optimize import fsolve

# pandas display using scientific notation

# pd.set_option('display.float_format', lambda x: f'{x:.3e}')

# use pint

units = UnitRegistry()
units.default_format = "~P.2f"

def to_decibels(arr, dc_gain = 0):
return np.log10(np.abs(arr)) * 20 + dc_gain

# Import Data

### I connected the oscilloscope leads between two terminals of the generator (the third

terminal was left dangling). I set the oscilloscope up with 2V/division (y axis) and 5s/division (time axis). That way, I got a trace which lasted more than 30 seconds, enough for it to slow down considerably. I used the data density setting of 12k data points, and this was easily able to capture all the peaks. I spun the turbine by hand by giving it a moderate shove. It started spinning with a frequency around 6Hz, and as it slowed down, I was able to capture its frequency and amplitude on the oscilloscope.

I captured one dataset with no load, and three further datasets at 100Ohm, 6.8Ohm, and (6.8 || (6.8 + 6.8)) Ohm loads between the terminals I was measuring.

# Plot Data

I calculated the frequency by looking at the spacing of the peaks. After smoothing out the

### frequency and the peak values, I found the location where each trace crossed 4Hz and took the amplitude at that location. Since the amplitude depends on frequency, this is to normalize across datasets, since the turbine is not necsessarily spinning at the same

frequency at the same timestamp.

In [ ]:
# Import data

(df_1, tspan, tstep) = helper.read_rigol_csv("oscilloscope_data/unloaded.csv", ch1 (df_2, tspan, tstep) = helper.read_rigol_csv("oscilloscope_data/100Ohm.csv", ch1 = (df_3, tspan, tstep) = helper.read_rigol_csv("oscilloscope_data/6_8Ohm.csv", ch1 = (df_4, tspan, tstep) = helper.read_rigol_csv("oscilloscope_data/4_5Ohm.csv", ch1 =

# Combine all variables into one for convenience

df = df_1.set_index("t").join([df_2.set_index("t"), df_3.set_index("t"), df_4.set_i # print(df.head(20))

In [ ]:

def moving_average(x, w):
w = int(w / 2) * 2
convolution = np.convolve(x, np.ones(w), 'full') / w
return convolution[int(w/2):-int(w/2)+1]

def find_y_crossing_monotonic_decrease(y_vals, y_target): left_side_idx = list(np.arange(len(y_vals))[y_vals > y_target]) return left_side_idx[-1]

def interpolate_outliers(y_vals, outlier_bool):
outlier_idx = np.nonzero(outlier_bool)[0]
if len(outlier_idx) == 0:
return y_vals
assert(all(np.diff(outlier_idx) > 1))
assert(all(outlier_idx > 0) and all(outlier_idx < len(y_vals - 1))) # not the f for idx in outlier_idx:
y_vals[idx] = (y_vals[idx - 1] + y_vals[idx + 1]) / 2
return y_vals

C:\Users\ieykamp\AppData\Local\Temp\ipykernel_13580\1153253338.py:36: PeakProperty Warning: some peaks have a width of 0
peak_idx = find_peaks(df_zoom[channel], distance = 25, width = 25)[0] C:\Users\ieykamp\AppData\Local\Temp\ipykernel_13580\1153253338.py:36: PeakProperty Warning: some peaks have a width of 0
peak_idx = find_peaks(df_zoom[channel], distance = 25, width = 25)[0] C:\Users\ieykamp\AppData\Local\Temp\ipykernel_13580\1153253338.py:36: PeakProperty Warning: some peaks have a width of 0
peak_idx = find_peaks(df_zoom[channel], distance = 25, width = 25)[0]

df_zoom = df[(df["t"] > 3) & (df["t"] < 25)]
fig, ((ax1, ax2), (ax3, ax4)) = plt.subplots(nrows = 2, ncols = 2, sharex = True, s fig.autofmt_xdate()

ax_list = [ax1, ax2, ax3, ax4]
channel_list = ["unloaded", "100Ohm", "6.8Ohm", "4.5Ohm"]
label_list = ["Unloaded", "100Ohm Load", "6.8Ohm Load", "4.5Ohm Load"]

amplitudes = []
for (ax, channel, label) in zip(ax_list, channel_list, label_list): helper.axes_labels("Oscilloscope timestamp", "s", "Voltage", "V", title = label

ax.plot(df_zoom["t"], df_zoom[channel], label = label)

# find peaks for frequency and envelope amplitude analysis

peak_idx = find_peaks(df_zoom[channel], distance = 25, width = 25)[0] df_peak_trace = df_zoom.iloc[peak_idx]
smooth_peaks = moving_average(df_peak_trace[channel], 10)

# find frequency using time difference between peaks

frequency = np.hstack((0, 1 / (np.diff(df_peak_trace["t"])))) smooth_frequency = moving_average(interpolate_outliers(frequency, frequency > 2

# find the envelope amplitude at a certain frequency for normalized comparison target_freq = 4 # Hz

target_freq_idx = find_y_crossing_monotonic_decrease(y_vals = smooth_frequency, amplitude_at_target_freq = smooth_peaks[target_freq_idx] amplitudes.append(amplitude_at_target_freq)

# plot peaks

ax.scatter(df_peak_trace["t"], df_peak_trace[channel]) ax.plot(df_peak_trace["t"], smooth_peaks, linestyle = "dashed", color = "green" ax.legend(loc = "upper right")

# plot frequency

rax = ax.twinx()
helper.axes_labels("Oscilloscope timestamp", "s", "Frequency", "Hz", title = la rax.plot(df_peak_trace["t"], smooth_frequency, color = "orange", label = "Frequ rax.set_ylim(0, 6.9)
rax.legend(loc = "lower right")


### The abrupt drop off in frequency near the end is a figment of the smoothing algorithm and

can be ignored.

The amplitudes at 4Hz are as follows. I calcualted the internal resistance | using the
following equation, based on the load resistor I was using: | , where
is the unloaded amplitude and | is the amplitude given a load resistor of | . The internal
resistance of the generator is approximately | .
| R1
| R1 = R2 ⋅ ( | − 1)
| Vin Vout | Vin
Vout | R2
| 14.5Ω ± 1Ω

In [ ]:
def calculate_R1(Vin, Vout, R2):
R1 = R2 * (Vin / Vout - 1)
return R1

print("Amplitude with no load at 4Hz =", np.round(amplitudes[0], 3) * units.volt) print("Amplitude with 100Ω load at 4Hz =", np.round(amplitudes[1], 3) * units.volt) print("Amplitude with 6.8Ω load at 4Hz =", np.round(amplitudes[2], 3) * units.volt) print("Amplitude with 4.5Ω load at 4Hz =", np.round(amplitudes[3], 3) * units.volt) print("")

print("Three different calculations for internal resistance:")
R1_100Ohm_test = calculate_R1(amplitudes[0] * units.volt, amplitudes[1] * units.vol print(f"R1 = {R1_100Ohm_test}")
R1_6_8Ohm_test = calculate_R1(amplitudes[0] * units.volt, amplitudes[2] * units.vol print(f"R1 = {R1_6_8Ohm_test}")
R1_4_5Ohm_test = calculate_R1(amplitudes[0] * units.volt, amplitudes[3] * units.vol print(f"R1 = {R1_4_5Ohm_test}")

R1 = np.mean(Quantity.from_list([R1_100Ohm_test, R1_6_8Ohm_test, R1_4_5Ohm_test])) print(f"Average R1 = {np.round(R1, 2)}")

Amplitude with no load at 4Hz = 1.17 V Amplitude with 100Ω load at 4Hz = 1.02 V
Amplitude with 6.8Ω load at 4Hz = 0.38 V
Amplitude with 4.5Ω load at 4Hz = 0.26 V

Three different calculations for internal resistance: R1 = 13.97 Ω
R1 = 14.17 Ω
R1 = 15.93 Ω
Average R1 = 14.69 ohm

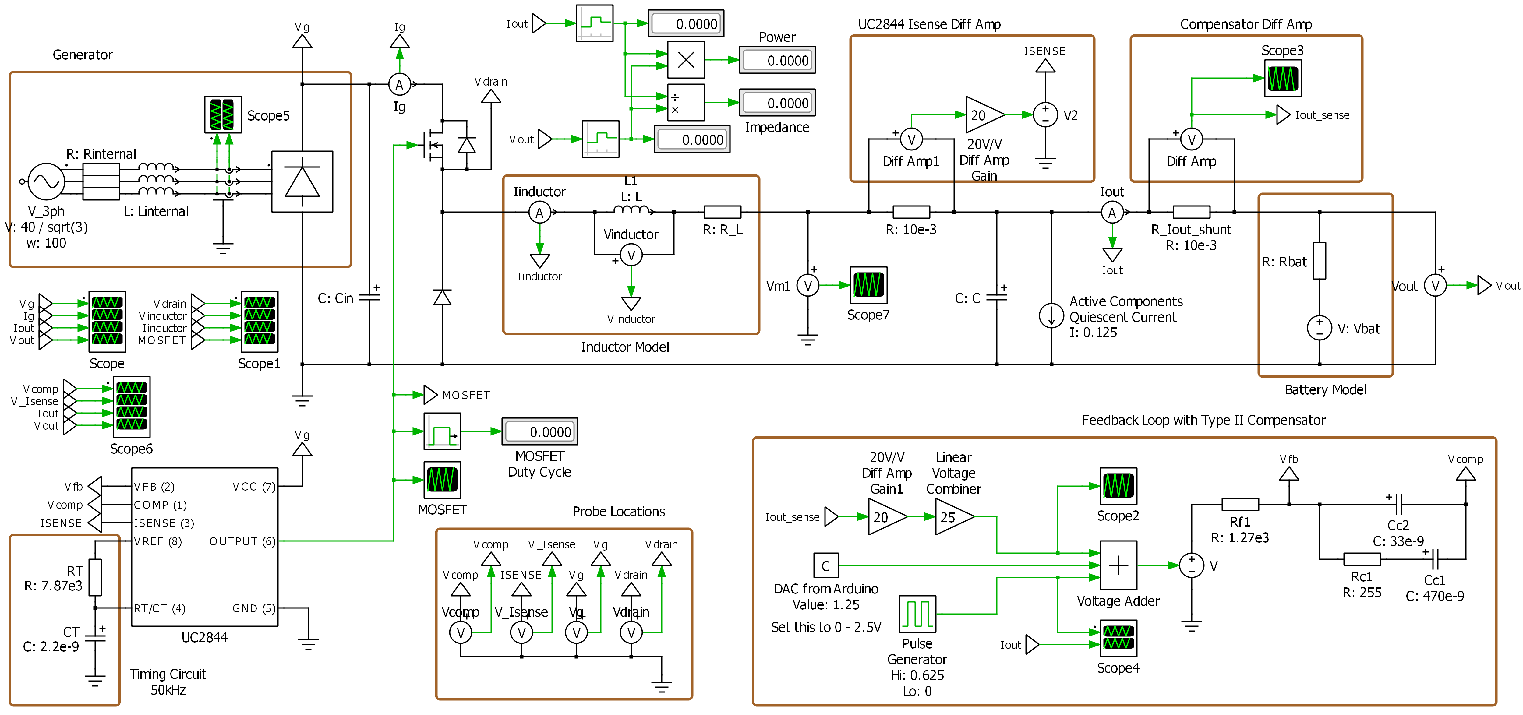
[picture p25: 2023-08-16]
small_wind_turbine/3phase_generator_buck_converter_schematic.png

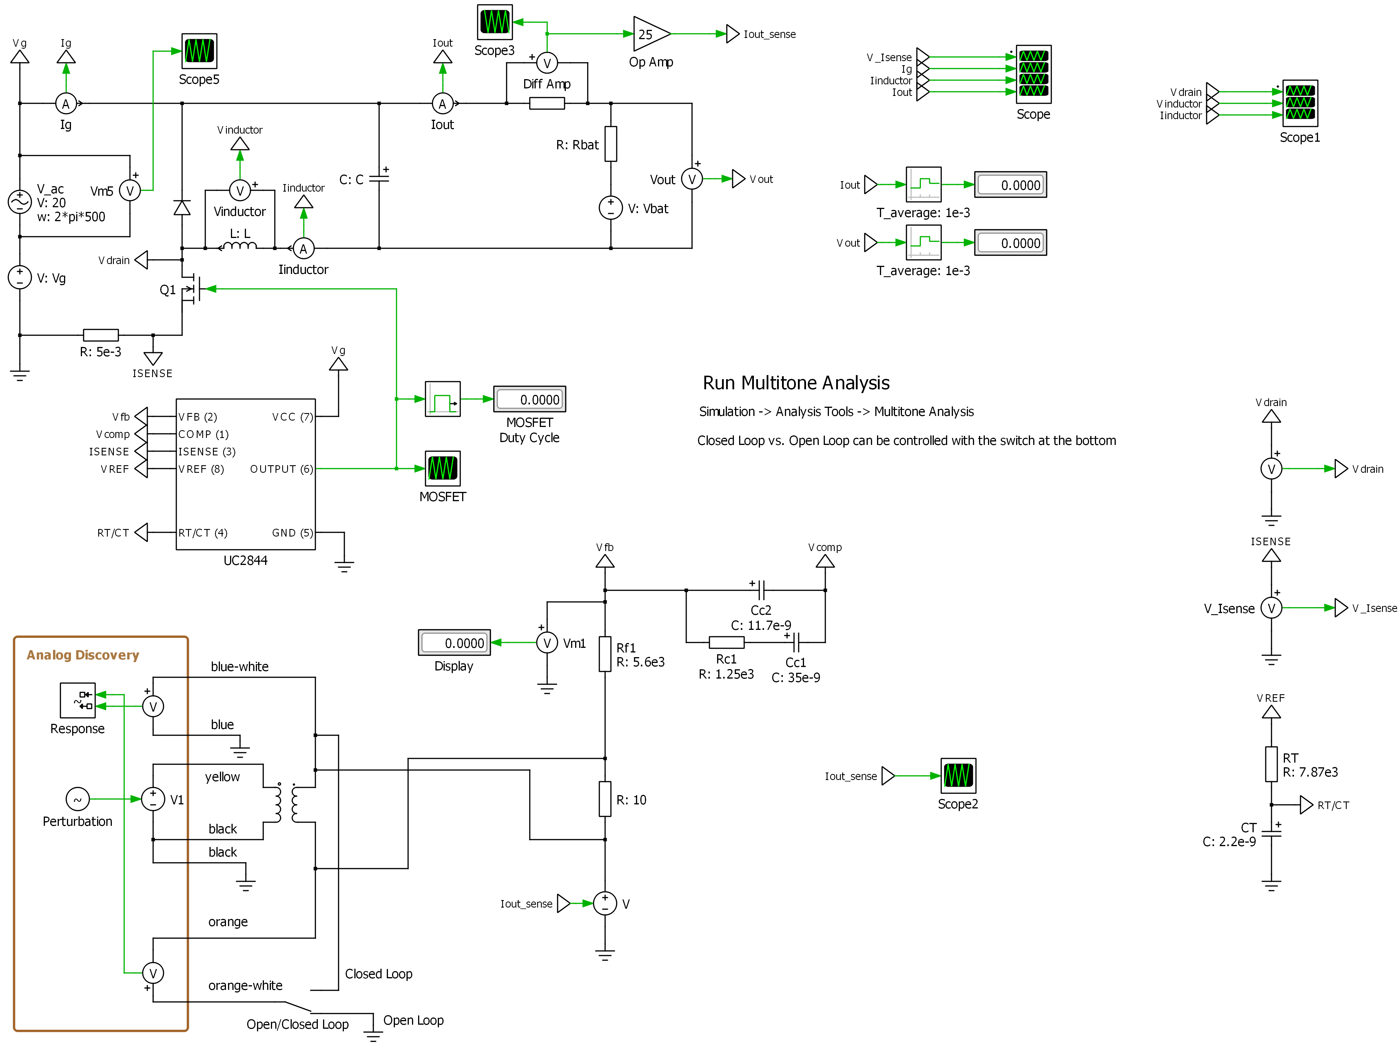
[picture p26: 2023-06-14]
small_wind_turbine/small_turbine_buck_converter_parameters/plecs_data/current_250mA/schematic_10a.png

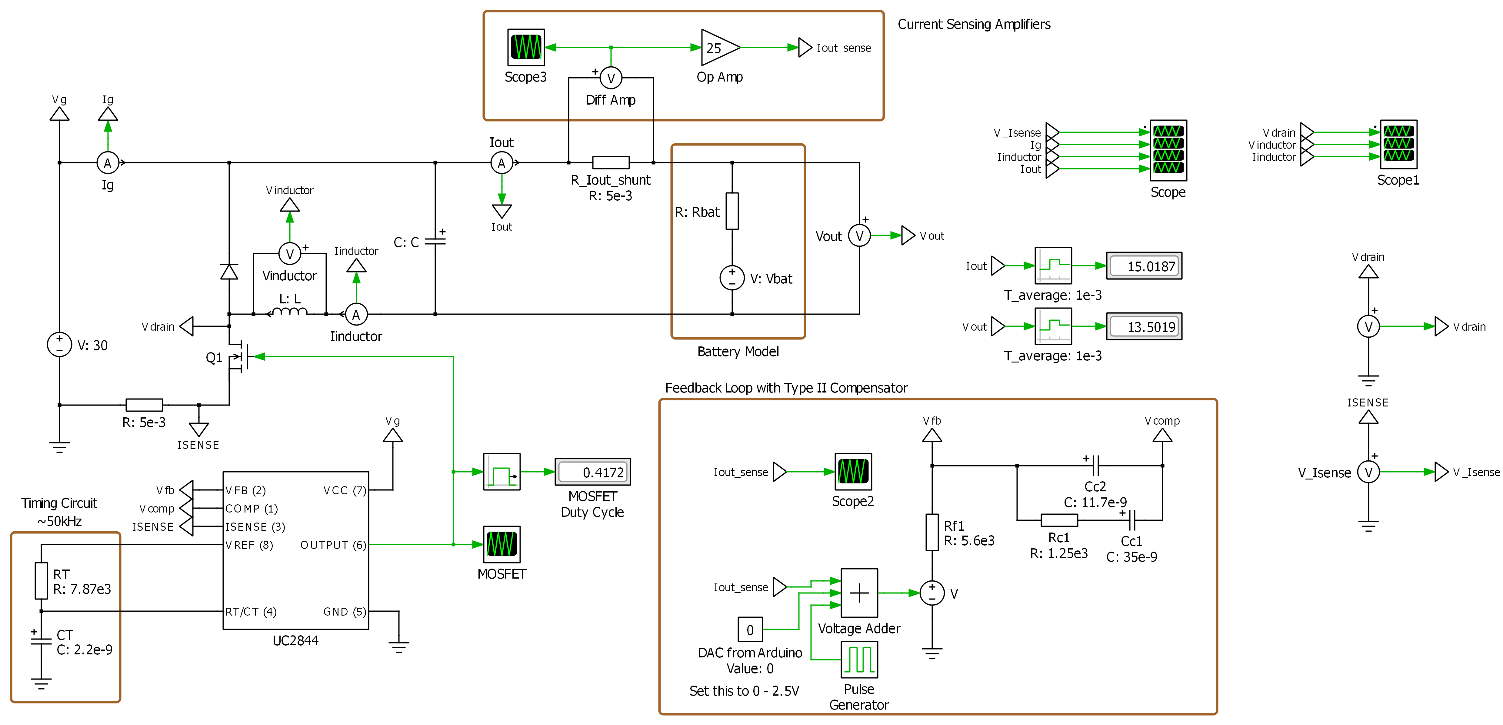
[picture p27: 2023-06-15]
small_wind_turbine/small_turbine_buck_converter_parameters/plecs_data/current_250mA/schematic_buck_converter_square_wave.png

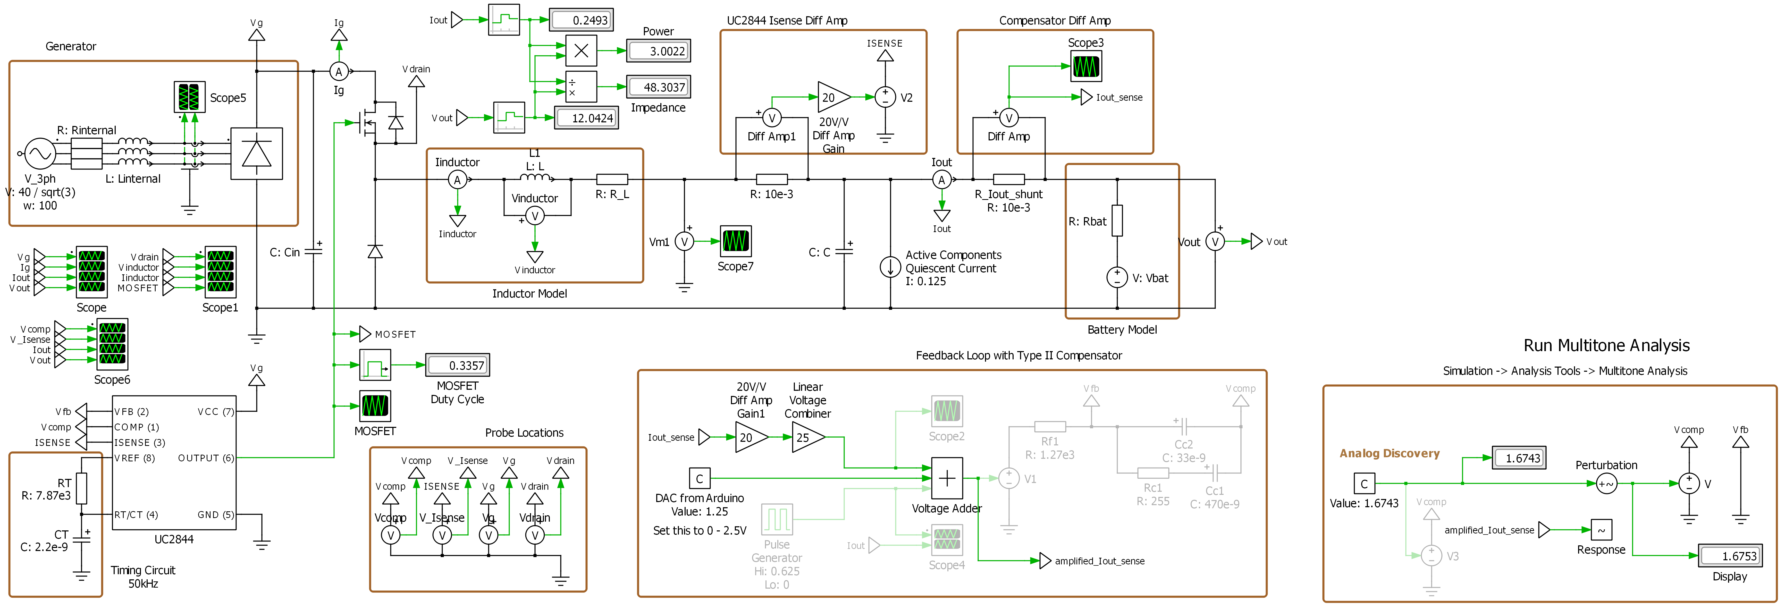
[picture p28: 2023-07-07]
small_wind_turbine/small_turbine_buck_converter_parameters/plecs_data/inductor_330uH/schematic_9a.png

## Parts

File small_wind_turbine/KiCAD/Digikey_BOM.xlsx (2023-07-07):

Index | Quantity | Part Number | Manufacturer Part Number | Description | Customer Reference | Available | Backorder | Unit Price | Extended Price USD
1 | 1 | Z3672-ND | G5LE-1-VDDC12 | RELAY GEN PURPOSE SPDT 10A 12V |  | 1 | 0 | 1.41 | 1.41
2 | 1 | EG2355-ND | 100SP1T1B4M2QE | SWITCH TOGGLE SPDT 5A 120V |  | 1 | 0 | 1.68 | 1.68
3 | 2 | 102-6406-ND | TBP01R1-508-02BE | TERMINAL BLOCK, PLUGGABLE, 5.08, |  | 2 | 0 | 0.56 | 1.12
4 | 2 | 102-6390-ND | TBP01P1-508-02BE | TERMINAL BLOCK, PLUGGABLE, 5.08 |  | 2 | 0 | 0.86 | 1.72
5 | 2 | 102-6407-ND | TBP01R1-508-03BE | TERMINAL BLOCK, PLUGGABLE, 5.08, |  | 2 | 0 | 0.61 | 1.22
6 | 2 | 102-6391-ND | TBP01P1-508-03BE | TERMINAL BLOCK, PLUGGABLE, 5.08 |  | 2 | 0 | 0.99 | 1.98
7 | 1 | 811-2464-ND | 60B334C | FIXED IND 330UH 4A 80 MOHM SMD |  | 1 | 0 | 2.2 | 2.20
8 | 10 | FSV10150VCT-ND | FSV10150V | DIODE SCHOTTKY 150V 10A TO277-3 |  | 10 | 0 | 0.713 | 7.13
9 | 1 | FDP61N20-ND | FDP61N20 | MOSFET N-CH 200V 61A TO220-3 |  | 1 | 0 | 2.86 | 2.86
10 | 3 | 296-47549-1-ND | TLV9064IDR | IC CMOS 4 CIRCUIT 14SOIC |  | 3 | 0 | 0.87 | 2.61
11 | 1 | 36-4527-ND | 4527 | FUSE HLDR CARTRIDGE 250V 5A PCB |  | 1 | 0 | 0.69 | 0.69
12 | 3 | 507-1263-ND | 5MF 1.5-R | FUSE GLASS 1.5A 250VAC 5X20MM |  | 3 | 0 | 0.61 | 1.83
13 | 1 | MCP4716A1T-E/CHCT-ND | MCP4716A1T-E/CH | IC DAC 10BIT V-OUT SOT23-6 |  | 1 | 0 | 1.08 | 1.08
14 | 1 | MCP3021A5T-E/OTCT-ND | MCP3021A5T-E/OT | IC ADC 10BIT SAR SOT23-5 |  | 1 | 0 | 1.41 | 1.41
15 | 1 | MCP3021A2T-E/OTCT-ND | MCP3021A2T-E/OT | IC ADC 10BIT SAR SOT23-5 |  | 1 | 0 | 1.41 | 1.41
16 | 3 | 160-1447-1-ND | LTST-C191KRKT | LED RED CLEAR SMD |  | 3 | 0 | 0.26 | 0.78
17 | 3 | 160-1446-1-ND | LTST-C191KGKT | LED GREEN CLEAR SMD |  | 3 | 0 | 0.26 | 0.78
18 | 5 | 160-1445-1-ND | LTST-C191KFKT | LED ORANGE CLEAR SMD |  | 5 | 0 | 0.24 | 1.20
19 | 3 | AZ1117IH-5.0TRG1DICT-ND | AZ1117IH-5.0TRG1 | IC REG LINEAR 5V 1A SOT223 |  | 3 | 0 | 0.37 | 1.11
20 | 1 | FVE300-16-ND | FVE030020E16R0KE | RES CHAS MNT 16 OHM 10% 300W |  | 1 | 0 | 22.05 | 22.05
21 | 1 | 505-LTC4440ES6#TRMPBFCT-ND | LTC4440ES6#TRMPBF | IC GATE DRVR HIGH-SIDE TSOT23-6 |  | 1 | 0 | 6.1 | 6.10
22 | 10 | S9337-ND | QPC02SXGN-RC | CONN JUMPER SHORTING .100" GOLD |  | 10 | 0 | 0.05 | 0.50
23 | 2 | 296-51172-1-ND | INA240A1DR | IC CURRENT SENSE 1 CIRCUIT 8SOIC |  | 2 | 0 | 3.3 | 6.60
24 | 1 | 565-4541-ND | EGXF101ELL201MK25S | CAP ALUM 200UF 20% 100V RAD TH |  | 1 | 0 | 2.24 | 2.24
25 | 1 | 399-18270-1-ND | ESK106M100AE3EA | CAP ALUM 10UF 20% 100V RADIAL |  | 1 | 0 | 0.24 | 0.24
26 | 4 | 4463-D1MPC1206QR010FF-T5CT-ND | D1MPC1206QR010FF-T5 | RES 0.01 OHM 1% 1W 1206 |  | 4 | 0 | 0.36 | 1.44
27 | 3 | RUC002N05T116CT-ND | RUC002N05T116 | MOSFET N-CH 50V 200MA SST3 |  | 3 | 0 | 0.32 | 0.96
28 | 1 | 493-12962-1-ND | UVY2C100MPD1TD | CAP ALUM 10UF 20% 160V RADIAL |  | 1 | 0 | 0.44 | 0.44
29 | 1 | SS16HECT-ND | SS16HE | DIODE SCHOTTKY 60V 1A SOD323HE |  | 1 | 0 | 0.42 | 0.42
30 | 12 | 490-18663-1-ND | GRM21BR61H106KE43L | CAP CER 10UF 50V X5R 0805 |  | 12 | 0 | 0.209 | 2.51
31 | 10 | 1276-6470-1-ND | CL21B105KBFNNNG | CAP CER 1UF 50V X7R 0805 |  | 10 | 0 | 0.079 | 0.79
32 | 20 | 1276-1003-1-ND | CL21B104KBCNNNC | CAP CER 0.1UF 50V X7R 0805 |  | 20 | 0 | 0.044 | 0.88
33 | 2 | 587-1288-1-ND | UMK212B7474KG-T | CAP CER 0.47UF 50V X7R 0805 |  | 2 | 0 | 0.26 | 0.52
34 | 2 | 445-7523-1-ND | C2012C0G1H333J125AA | CAP CER 0.033UF 50V C0G 0805 |  | 2 | 0 | 0.33 | 0.66
35 | 2 | 1276-6492-1-ND | CL21C222JBFNNNG | CAP CER 2200PF 50V C0G/NP0 0805 |  | 2 | 0 | 0.11 | 0.22
36 | 10 | A130138CT-ND | CRGCQ0805J4K7 | RES 4.7K OHM 5% 1/8W 0805 |  | 10 | 0 | 0.036 | 0.36
37 | 10 | 311-12.0KCRCT-ND | RC0805FR-0712KL | RES 12K OHM 1% 1/8W 0805 |  | 10 | 0 | 0.025 | 0.25
38 | 10 | 13-RC0805FR-103KLCT-ND | RC0805FR-103KL | RES 3K OHM 1% 1/8W 0805 |  | 10 | 0 | 0.024 | 0.24
39 | 2 | P82KDACT-ND | ERA-6AEB823V | RES 82K OHM 0.1% 1/8W 0805 |  | 2 | 0 | 0.33 | 0.66
40 | 2 | P20720CT-ND | ERJ-PB6B1302V | RES SMD 13K OHM 0.1% 1/4W 0805 |  | 2 | 0 | 0.36 | 0.72
41 | 10 | 13-RC0805FR-10200RLCT-ND | RC0805FR-10200RL | RES 200 OHM 1% 1/8W 0805 |  | 10 | 0 | 0.024 | 0.24
42 | 10 | 13-RC0805FR-131KLCT-ND | RC0805FR-131KL | RES 1K OHM 1% 1/8W 0805 |  | 10 | 0 | 0.024 | 0.24
43 | 2 | RHM10.0AECT-ND | ESR10EZPF10R0 | RES SMD 10 OHM 1% 0.4W 0805 |  | 2 | 0 | 0.2 | 0.40
44 | 10 | 311-300ARCT-ND | RC0805JR-07300RL | RES 300 OHM 5% 1/8W 0805 |  | 10 | 0 | 0.022 | 0.22
45 | 10 | 311-130ARCT-ND | RC0805JR-07130RL | RES 130 OHM 5% 1/8W 0805 |  | 10 | 0 | 0.022 | 0.22
46 | 10 | 311-255CRCT-ND | RC0805FR-07255RL | RES 255 OHM 1% 1/8W 0805 |  | 10 | 0 | 0.024 | 0.24
47 | 10 | 311-1.27KCRCT-ND | RC0805FR-071K27L | RES 1.27K OHM 1% 1/8W 0805 |  | 10 | 0 | 0.024 | 0.24
48 | 10 | 311-7.87KCRCT-ND | RC0805FR-077K87L | RES 7.87K OHM 1% 1/8W 0805 |  | 10 | 0 | 0.024 | 0.24

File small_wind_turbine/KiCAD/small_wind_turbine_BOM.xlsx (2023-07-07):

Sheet: Final BOM
This sheet is the BOM for the small wind turbine battery charger PCB. All of these components can be found on Digikey except for the very first row, which is only available on Mouser. Quantity is intelligently over-estimated so we can assume some parts will fail or get lost and still be able to make the board. See the other sheets in this document for the raw component quantities listed in the schematic.
Row | Checked | Part Name | Quantity | Supplier | Link | Datasheet | Price per ($) | Total price ($)
0 | TRUE | UC2844 | 1 | Mouser | https://www.mouser.com/ProductDetail/Texas-Instruments/UC2844AD8?qs=xJkDX%2FqrskO30lVwYIVmGA%3D%3D | https://www.ti.com/lit/ds/symlink/uc2844a.pdf | 1.4 | 1.4
1 | TRUE | SPDT Relay | 1 | Digikey | https://www.digikey.com/en/products/detail/omron-electronics-inc-emc-div/G5LE-1-VDDC12/1815685 | https://omronfs.omron.com/en_US/ecb/products/pdf/en-g5le.pdf | 1.41 | 1.41
2 | TRUE | Manual Switch | 1 | Digikey | https://www.digikey.com/en/products/detail/e-switch/100SP1T1B4M2QE/378824 |  | 1.68 | 1.68
3 | TRUE | Terminal Block 2 Pin F | 2 | Digikey | https://www.digikey.com/en/products/detail/cui-devices/TBP01R1-508-02BE/10238383 |  | 0.56 | 1.12
4 | TRUE | Terminal Block 2 Pin M | 2 | Digikey | https://www.digikey.com/en/products/detail/cui-devices/TBP01P1-508-02BE/10238367 |  | 0.86 | 1.72
5 | TRUE | Terminal Block 3 Pin F | 2 | Digikey | https://www.digikey.com/en/products/detail/cui-devices/TBP01R1-508-03BE/10238384 |  | 0.61 | 1.22
6 | TRUE | Terminal Block 3 Pin M | 2 | Digikey | https://www.digikey.com/en/products/detail/cui-devices/TBP01P1-508-03BE/10238368 |  | 0.99 | 1.98
7 | TRUE | Power Inductor 330uH | 1 | Digikey | https://www.digikey.com/en/products/detail/murata-power-solutions-inc/60B334C/3178535 | https://search.murata.co.jp/Ceramy/image/img/P02A/kmp_6000b.pdf | 2.2 | 2.2
8 | TRUE | Bridge Rectifer Diode | 10 | Digikey | https://www.digikey.com/en/products/detail/onsemi/FSV10150V/5306658 | https://www.onsemi.com/pdf/datasheet/fsv10150v-d.pdf | 0.713 | 7.13
9 | TRUE | Switching MOSFET | 1 | Digikey | https://www.digikey.com/en/products/detail/onsemi/FDP61N20/1217877 | https://www.onsemi.com/pdf/datasheet/fdp61n20-d.pdf | 2.86 | 2.86
10 | TRUE | Op Amp Quad | 3 | Digikey | https://www.digikey.com/en/products/detail/texas-instruments/TLV9064IDR/7931882 | https://www.ti.com/lit/ds/symlink/tlv9064.pdf | 0.87 | 2.61
11 | TRUE | Fuse Holder, 5x20mm | 1 | Digikey | https://www.digikey.com/en/products/detail/keystone-electronics/4527/8397 |  | 0.69 | 0.69
12 | TRUE | 1.5A Fuse, 5x20mm | 3 | Digikey | https://www.digikey.com/en/products/detail/bel-fuse-inc/5MF-1-5-R/1009035 |  | 0.61 | 1.83
13 | TRUE | SPI 10-bit DAC | 1 | Digikey | https://www.digikey.com/en/products/detail/microchip-technology/MCP4716A1T-E-CH/2665073 | https://ww1.microchip.com/downloads/en/DeviceDoc/22272C.pdf | 1.08 | 1.08
14 | TRUE | I2C 10-bit ADC Address 5 | 1 | Digikey | https://www.digikey.com/en/products/detail/microchip-technology/MCP3021A5T-E-OT/593685 | https://ww1.microchip.com/downloads/aemDocuments/documents/APID/ProductDocuments/DataSheets/20001805C.pdf | 1.41 | 1.41
15 | TRUE | I2C 10-bit ADC Address 2 | 1 | Digikey | https://www.digikey.com/en/products/detail/microchip-technology/MCP3021A2T-E-OT/2601424 | https://ww1.microchip.com/downloads/aemDocuments/documents/APID/ProductDocuments/DataSheets/20001805C.pdf | 1.41 | 1.41
16 | TRUE | Orange LEDs | 3 | Digikey | https://www.digikey.com/en/products/detail/liteon/LTST-C191KFKT/386833 |  | 0.26 | 0.78
17 | TRUE | Green LEDs | 3 | Digikey | https://www.digikey.com/en/products/detail/liteon/LTST-C191KGKT/386835 |  | 0.26 | 0.78
18 | TRUE | Red LEDs | 5 | Digikey | https://www.digikey.com/en/products/detail/liteon/LTST-C191KRKT/386837 |  | 0.24 | 1.2
19 | TRUE | 5V Linear Regulator | 3 | Digikey | https://www.digikey.com/en/products/detail/diodes-incorporated/AZ1117IH-5-0TRG1/5699673 | https://www.diodes.com/assets/Datasheets/AZ1117I.pdf | 0.37 | 1.11
20 | TRUE | Dump Load Resistor | 1 | Digikey | https://www.digikey.com/en/products/detail/vishay-huntington-electric-inc/FVE030020E16R0KE/269993 |  | 22.05 | 22.05
21 | TRUE | High Side Gate Driver Opt. 2 | 1 | Digikey | https://www.digikey.com/en/products/detail/analog-devices-inc/LTC4440ES6-TRMPBF/1116021 | https://www.analog.com/media/en/technical-documentation/data-sheets/4440fb.pdf | 6.1 | 6.1
22 | TRUE | 2-pin Jumpers | 10 | Digikey | https://www.digikey.com/en/products/detail/sullins-connector-solutions/QPC02SXGN-RC/2618262 |  | 0.05 | 0.5
23 | TRUE | Differential Amplifier Opt. 2 | 2 | Digikey | https://www.digikey.com/en/products/detail/texas-instruments/INA240A1DR/8538109 | https://www.ti.com/lit/ds/symlink/ina240.pdf | 3.3 | 6.6
24 | TRUE | 200uF Aluminum Capacitor | 1 | Digikey | https://www.digikey.com/en/products/detail/chemi-con/EGXF101ELL201MK25S/6204522 |  | 2.24 | 2.24
25 | TRUE | 10uF Aluminum Capacitor | 1 | Digikey | https://www.digikey.com/en/products/detail/kemet/ESK106M100AE3EA/9448267 |  | 0.24 | 0.24
26 | TRUE | 10mOhm 1206 Resistor | 4 | Digikey | https://www.digikey.com/en/products/detail/thin-film-technology-corp/D1MPC1206QR010FF-T5/16735470 |  | 0.36 | 1.44
27 | TRUE | Relay MOSFET | 3 | Digikey | https://www.digikey.com/en/products/detail/rohm-semiconductor/RUC002N05T116/4004578 | https://fscdn.rohm.com/en/products/databook/datasheet/discrete/transistor/mosfet/ruc002n05t116-e.pdf | 0.32 | 0.96
28 | TRUE | 10uF Jumper Capacitor | 1 | Digikey | https://www.digikey.com/en/products/detail/nichicon/UVY2C100MPD1TD/4329161 |  | 0.44 | 0.44
29 | TRUE | Relay Diode | 1 | Digikey | https://www.digikey.com/en/products/detail/onsemi/SS16HE/6009695 | https://www.onsemi.com/pdf/datasheet/ss13he-d.pdf | 0.42 | 0.42
30 | TRUE | 10uF 0805 Capacitor | 12 | Digikey | https://www.digikey.com/en/products/detail/murata-electronics/GRM21BR61H106KE43L/10326316 |  | 0.209 | 2.51
31 | TRUE | 1uF 0805 Capacitor | 10 | Digikey | https://www.digikey.com/en/products/detail/samsung-electro-mechanics/CL21B105KBFNNNG/3894467 |  | 0.079 | 0.79
32 | TRUE | 0.1uF 0805 Capacitor | 20 | Digikey | https://www.digikey.com/en/products/detail/samsung-electro-mechanics/CL21B104KBCNNNC/3886661 |  | 0.044 | 0.88
33 | TRUE | 470nF 0805 Capacitor | 2 | Digikey | https://www.digikey.com/en/products/detail/taiyo-yuden/UMK212B7474KG-T/930640 |  | 0.26 | 0.52
34 | TRUE | 33nF 0805 Capacitor | 2 | Digikey | https://www.digikey.com/en/products/detail/tdk-corporation/C2012C0G1H333J125AA/2732958 |  | 0.33 | 0.66
35 | TRUE | 2.2nF 0805 Capacitor | 2 | Digikey | https://www.digikey.com/en/products/detail/samsung-electro-mechanics/CL21C222JBFNNNG/3894586 |  | 0.11 | 0.22
36 | TRUE | 4.7k Ohm 0805 Resistor | 10 | Digikey | https://www.digikey.com/en/products/detail/te-connectivity-passive-product/CRGCQ0805J4K7/8576740 |  | 0.036 | 0.36
37 | TRUE | 12k Ohm 0805 Resistor | 10 | Digikey | https://www.digikey.com/en/products/detail/yageo/RC0805FR-0712KL/727568 |  | 0.025 | 0.25
38 | TRUE | 3k Ohm 0805 Resistor | 10 | Digikey | https://www.digikey.com/en/products/detail/yageo/RC0805FR-103KL/14286566 |  | 0.024 | 0.24
39 | TRUE | 82k Ohm 0805 Resistor | 2 | Digikey | https://www.digikey.com/en/products/detail/panasonic-electronic-components/ERA-6AEB823V/1465795 |  | 0.33 | 0.66
40 | TRUE | 13k Ohm 0805 Resistor | 2 | Digikey | https://www.digikey.com/en/products/detail/panasonic-electronic-components/ERJ-PB6B1302V/6213503 |  | 0.36 | 0.72
41 | TRUE | 200 Ohm 0805 Resistor | 10 | Digikey | https://www.digikey.com/en/products/detail/yageo/RC0805FR-10200RL/14286525 |  | 0.024 | 0.24
42 | TRUE | 1k Ohm 0805 Resistor | 10 | Digikey | https://www.digikey.com/en/products/detail/yageo/RC0805FR-131KL/13694082 |  | 0.024 | 0.24
43 | TRUE | 10 Ohm 0805 Resistor | 2 | Digikey | https://www.digikey.com/en/products/detail/rohm-semiconductor/ESR10EZPF10R0/1983483 |  | 0.2 | 0.4
44 | TRUE | 300 Ohm 0805 Resistor | 10 | Digikey | https://www.digikey.com/en/products/detail/yageo/RC0805JR-07300RL/728307 |  | 0.022 | 0.22
45 | TRUE | 130 Ohm 0805 Resistor | 10 | Digikey | https://www.digikey.com/en/products/detail/yageo/RC0805JR-07130RL/728251 |  | 0.022 | 0.22
46 | TRUE | 255 Ohm 0805 Resistor | 10 | Digikey | https://www.digikey.com/en/products/detail/yageo/RC0805FR-07255RL/727769 |  | 0.024 | 0.24
47 | TRUE | 1.27k Ohm 0805 Resistor | 10 | Digikey | https://www.digikey.com/en/products/detail/yageo/RC0805FR-071K27L/727475 |  | 0.024 | 0.24
48 | TRUE | 7.87k Ohm 0805 Resistor | 10 | Digikey | https://www.digikey.com/en/products/detail/yageo/RC0805FR-077K87L/728122 |  | 0.024 | 0.24
Total: |  |  | 226 Parts |  |  |  | Total: | $ 86.46

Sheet: Estimating Quantities
This sheet is the BOM for the small wind turbine battery charger PCB. I have specced components for ~2A maximum current draw into a 12V marine battery. All of these components can be found on Digikey unless otherwise noted. Quantity is required for making one PCB; it is the actual components listed in the schematic. We may want to order enough for 2 PCB's. |  |  |  |  |  |  |  |  | Quantity (including extras of small and cheap components) | Price (including extras of small and cheap components) | Quantity (including enough for 2 PCBs and some extras) | Price (including enough for 2 PCBs and some extras)
Row | Checked | Part Name | Quantity | Supplier | Link | Datasheet | Price per ($) | Total price ($)
1 | TRUE | SPDT Relay | 1 | Digikey | https://www.digikey.com/en/products/detail/omron-electronics-inc-emc-div/G5LE-1-VDDC12/1815685 | https://omronfs.omron.com/en_US/ecb/products/pdf/en-g5le.pdf | 1.41 | 1.41 | 1 | 1.41 | 2 | 2.82
2 | TRUE | Manual Switch | 1 | Digikey | https://www.digikey.com/en/products/detail/e-switch/100SP1T1B4M2QE/378824 |  | 1.68 | 1.68 | 1 | 1.68 | 2 | 3.36
3 | TRUE | Terminal Block 2 Pin F | 2 | Digikey | https://www.digikey.com/en/products/detail/cui-devices/TBP01R1-508-02BE/10238383 |  | 0.56 | 1.12 | 2 | 1.12 | 4 | 2.24
4 | TRUE | Terminal Block 2 Pin M | 2 | Digikey | https://www.digikey.com/en/products/detail/cui-devices/TBP01P1-508-02BE/10238367 |  | 0.86 | 1.72 | 2 | 1.72 | 4 | 3.44
5 | TRUE | Terminal Block 3 Pin F | 2 | Digikey | https://www.digikey.com/en/products/detail/cui-devices/TBP01R1-508-03BE/10238384 |  | 0.61 | 1.22 | 2 | 1.22 | 4 | 2.44
6 | TRUE | Terminal Block 3 Pin M | 2 | Digikey | https://www.digikey.com/en/products/detail/cui-devices/TBP01P1-508-03BE/10238368 |  | 0.99 | 1.98 | 2 | 1.98 | 4 | 3.96
7 | TRUE | Power Inductor 330uH | 1 | Digikey | https://www.digikey.com/en/products/detail/murata-power-solutions-inc/60B334C/3178535 | https://search.murata.co.jp/Ceramy/image/img/P02A/kmp_6000b.pdf | 2.2 | 2.2 | 1 | 2.2 | 2 | 4.4
8 | TRUE | Bridge Rectifer Diode | 8 | Digikey | https://www.digikey.com/en/products/detail/onsemi/FSV10150V/5306658 | https://www.onsemi.com/pdf/datasheet/fsv10150v-d.pdf | 0.81 | 6.48 | 10 | 8.1 | 20 | 16.2
9 | TRUE | Switching MOSFET | 1 | Digikey | https://www.digikey.com/en/products/detail/onsemi/FDP61N20/1217877 | https://www.onsemi.com/pdf/datasheet/fdp61n20-d.pdf | 2.86 | 2.86 | 1 | 2.86 | 2 | 5.72
10 | TRUE | Op Amp Quad | 1 | Digikey | https://www.digikey.com/en/products/detail/texas-instruments/TLV9064IDR/7931882 | https://www.ti.com/lit/ds/symlink/tlv9064.pdf | 0.87 | 0.87 | 3 | 2.61 | 6 | 5.22
11 | TRUE | Fuse Holder, 5x20mm | 1 | Digikey | https://www.digikey.com/en/products/detail/keystone-electronics/4527/8397 |  | 0.69 | 0.69 | 1 | 0.69 | 2 | 1.38
12 | TRUE | 1.5A Fuse, 5x20mm | 1 | Digikey | https://www.digikey.com/en/products/detail/bel-fuse-inc/5MF-1-5-R/1009035 |  | 0.61 | 0.61 | 3 | 1.83 | 6 | 3.66
13 | TRUE | UC2844 | 1 | Mouser | https://www.mouser.com/ProductDetail/Texas-Instruments/UC2844AD8?qs=xJkDX%2FqrskO30lVwYIVmGA%3D%3D | https://www.ti.com/lit/ds/symlink/uc2844a.pdf | 1.59 | 1.59 | 1 | 1.59 | 2 | 3.18
14 | TRUE | SPI 10-bit DAC | 1 | Digikey | https://www.digikey.com/en/products/detail/microchip-technology/MCP4716A1T-E-CH/2665073 | https://ww1.microchip.com/downloads/en/DeviceDoc/22272C.pdf | 1.08 | 1.08 | 1 | 1.08 | 2 | 2.16
15 | TRUE | I2C 10-bit ADC Address 5 | 1 | Digikey | https://www.digikey.com/en/products/detail/microchip-technology/MCP3021A5T-E-OT/593685 | https://ww1.microchip.com/downloads/aemDocuments/documents/APID/ProductDocuments/DataSheets/20001805C.pdf | 1.41 | 1.41 | 1 | 1.41 | 2 | 2.82
16 | TRUE | I2C 10-bit ADC Address 2 | 1 | Digikey | https://www.digikey.com/en/products/detail/microchip-technology/MCP3021A2T-E-OT/2601424 | https://ww1.microchip.com/downloads/aemDocuments/documents/APID/ProductDocuments/DataSheets/20001805C.pdf | 1.41 | 1.41 | 1 | 1.41 | 2 | 2.82
17 | TRUE | Orange LEDs | 4 | Digikey | https://www.digikey.com/en/products/detail/liteon/LTST-C191KFKT/386833 |  | 0.24 | 0.96 | 5 | 1.2 | 10 | 2.4
18 | TRUE | Green LEDs | 1 | Digikey | https://www.digikey.com/en/products/detail/liteon/LTST-C191KGKT/386835 |  | 0.26 | 0.26 | 3 | 0.78 | 5 | 1.3
19 | TRUE | Red LEDs | 1 | Digikey | https://www.digikey.com/en/products/detail/liteon/LTST-C191KRKT/386837 |  | 0.26 | 0.26 | 3 | 0.78 | 5 | 1.3
20 | TRUE | 5V Linear Regulator | 1 | Digikey | https://www.digikey.com/en/products/detail/diodes-incorporated/AZ1117IH-5-0TRG1/5699673 | https://www.diodes.com/assets/Datasheets/AZ1117I.pdf | 0.37 | 0.37 | 3 | 1.11 | 5 | 1.85
21 | TRUE | Dump Load Resistor | 1 | Digikey | https://www.digikey.com/en/products/detail/vishay-huntington-electric-inc/FVE030020E16R0KE/269993 |  | 22.05 | 22.05 | 1 | 22.05 | 1 | 22.05
22 | TRUE | High Side Gate Driver Opt. 2 | 1 | Digikey | https://www.digikey.com/en/products/detail/analog-devices-inc/LTC4440ES6-TRMPBF/1116021 | https://www.analog.com/media/en/technical-documentation/data-sheets/4440fb.pdf | 6.04 | 6.04 | 1 | 6.04 | 2 | 12.08
23 | TRUE | 2-pin Jumpers | 10 | Digikey | https://www.digikey.com/en/products/detail/sullins-connector-solutions/QPC02SXGN-RC/2618262 |  | 0.1 | 1 | 10 | 1 | 20 | 2
24 | TRUE | Differential Amplifier Opt. 2 | 2 | Digikey | https://www.digikey.com/en/products/detail/texas-instruments/INA240A1DR/8538109 | https://www.ti.com/lit/ds/symlink/ina240.pdf | 3.3 | 6.6 | 2 | 6.6 | 4 | 13.2
25 | TRUE | 200uF Aluminum Capacitor | 1 | Digikey | https://www.digikey.com/en/products/detail/chemi-con/EGXF101ELL201MK25S/6204522 |  | 2.3 | 2.3 | 1 | 2.3 | 2 | 4.6
26 | TRUE | 10uF Aluminum Capacitor | 1 | Digikey | https://www.digikey.com/en/products/detail/kemet/ESK106M100AE3EA/9448267 |  | 0.25 | 0.25 | 1 | 0.25 | 2 | 0.5
27 | TRUE | 10mOhm 1206 Resistor | 2 | Digikey | https://www.digikey.com/en/products/detail/thin-film-technology-corp/D1MPC1206QR010FF-T5/16735470 |  | 0.36 | 0.72 | 4 | 1.44 | 8 | 2.88
28 | TRUE | Relay MOSFET | 1 | Digikey | https://www.digikey.com/en/products/detail/rohm-semiconductor/RUC002N05T116/4004578 | https://fscdn.rohm.com/en/products/databook/datasheet/discrete/transistor/mosfet/ruc002n05t116-e.pdf | 0.32 | 0.32 | 3 | 0.96 | 6 | 1.92
29 | TRUE | 10uF Jumper Capacitor | 1 | Digikey | https://www.digikey.com/en/products/detail/nichicon/UVY2C100MPD1TD/4329161 |  | 0.68 | 0.68 | 1 | 0.68 | 2 | 1.36
30 | TRUE | Relay Diode | 1 | Digikey | https://www.digikey.com/en/products/detail/onsemi/SS16HE/6009695 | https://www.onsemi.com/pdf/datasheet/ss13he-d.pdf | 0.42 | 0.42 | 1 | 0.42 | 2 | 0.84
31 | TRUE | 10uF 0805 Capacitor | 6 | Digikey | https://www.digikey.com/en/products/detail/murata-electronics/GRM21BR61H106KE43L/10326316 |  | 0.3 | 1.8 | 12 | 3.6 | 24 | 7.2
32 | TRUE | 1uF 0805 Capacitor | 3 | Digikey | https://www.digikey.com/en/products/detail/samsung-electro-mechanics/CL21B105KBFNNNG/3894467 |  | 0.11 | 0.33 | 10 | 1.1 | 20 | 2.2
33 | TRUE | 0.1uF 0805 Capacitor | 9 | Digikey | https://www.digikey.com/en/products/detail/samsung-electro-mechanics/CL21B104KBCNNNC/3886661 |  | 0.1 | 0.9 | 20 | 2 | 40 | 4
34 | TRUE | 470nF 0805 Capacitor | 1 | Digikey | https://www.digikey.com/en/products/detail/taiyo-yuden/UMK212B7474KG-T/930640 |  | 0.26 | 0.26 | 2 | 0.52 | 4 | 1.04
35 | TRUE | 33nF 0805 Capacitor | 1 | Digikey | https://www.digikey.com/en/products/detail/tdk-corporation/C2012C0G1H333J125AA/2732958 |  | 0.3 | 0.3 | 2 | 0.6 | 4 | 1.2
36 | TRUE | 2.2nF 0805 Capacitor | 1 | Digikey | https://www.digikey.com/en/products/detail/samsung-electro-mechanics/CL21C222JBFNNNG/3894586 |  | 0.11 | 0.11 | 2 | 0.22 | 4 | 0.44
37 | TRUE | 4.7k Ohm 0805 Resistor | 4 | Digikey | https://www.digikey.com/en/products/detail/te-connectivity-passive-product/CRGCQ0805J4K7/8576740 |  | 0.1 | 0.4 | 10 | 1 | 20 | 2
38 | TRUE | 12k Ohm 0805 Resistor | 1 | Digikey | https://www.digikey.com/en/products/detail/yageo/RC0805FR-0712KL/727568 |  | 0.1 | 0.1 | 2 | 0.2 | 4 | 0.4
39 | TRUE | 3k Ohm 0805 Resistor | 1 | Digikey | https://www.digikey.com/en/products/detail/yageo/RC0805FR-103KL/14286566 |  | 0.1 | 0.1 | 2 | 0.2 | 4 | 0.4
40 | TRUE | 82k Ohm 0805 Resistor | 1 | Digikey | https://www.digikey.com/en/products/detail/panasonic-electronic-components/ERA-6AEB823V/1465795 |  | 0.33 | 0.33 | 2 | 0.66 | 4 | 1.32
41 | TRUE | 13k Ohm 0805 Resistor | 1 | Digikey | https://www.digikey.com/en/products/detail/panasonic-electronic-components/ERJ-PB6B1302V/6213503 |  | 0.36 | 0.36 | 2 | 0.72 | 4 | 1.44
42 | TRUE | 200 Ohm 0805 Resistor | 2 | Digikey | https://www.digikey.com/en/products/detail/yageo/RC0805FR-10200RL/14286525 |  | 0.1 | 0.2 | 10 | 1 | 20 | 2
43 | TRUE | 1k Ohm 0805 Resistor | 2 | Digikey | https://www.digikey.com/en/products/detail/yageo/RC0805FR-131KL/13694082 |  | 0.1 | 0.2 | 10 | 1 | 20 | 2
44 | TRUE | 10 Ohm 0805 Resistor | 1 | Digikey | https://www.digikey.com/en/products/detail/rohm-semiconductor/ESR10EZPF10R0/1983483 |  | 0.2 | 0.2 | 2 | 0.4 | 4 | 0.8
45 | TRUE | 300 Ohm 0805 Resistor | 1 | Digikey | https://www.digikey.com/en/products/detail/yageo/RC0805JR-07300RL/728307 |  | 0.1 | 0.1 | 2 | 0.2 | 4 | 0.4
46 | TRUE | 130 Ohm 0805 Resistor | 4 | Digikey | https://www.digikey.com/en/products/detail/yageo/RC0805JR-07130RL/728251 |  | 0.1 | 0.4 | 10 | 1 | 20 | 2
47 | TRUE | 255 Ohm 0805 Resistor | 1 | Digikey | https://www.digikey.com/en/products/detail/yageo/RC0805FR-07255RL/727769 |  | 0.1 | 0.1 | 2 | 0.2 | 4 | 0.4
48 | TRUE | 1.27k Ohm 0805 Resistor | 1 | Digikey | https://www.digikey.com/en/products/detail/yageo/RC0805FR-071K27L/727475 |  | 0.1 | 0.1 | 2 | 0.2 | 4 | 0.4
49 | TRUE | 7.87k Ohm 0805 Resistor | 1 | Digikey | https://www.digikey.com/en/products/detail/yageo/RC0805FR-077K87L/728122 |  | 0.1 | 0.1 | 2 | 0.2 | 4 | 0.4
Total: |  |  | 97 Parts |  |  |  | Total: | $ 76.95 | 178 Components | $ 93.54 | 352 Components | $ 164.14
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

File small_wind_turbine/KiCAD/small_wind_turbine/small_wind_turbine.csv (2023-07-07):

Source: | C:\dev\git\wind-turbine\small_wind_turbine\KiCAD\small_wind_turbine\small_wind_turbine.kicad_sch
Date: | 7/6/2023 11:22:20 AM
Tool: | Eeschema (6.0.7)
Generator: | C:\Program Files\KiCad\6.0\bin\scripting\plugins/bom_csv_grouped_by_value_with_fp.py
Component Count: | 95
Ref | Qnty | Value | Cmp name | Footprint | Description | Vendor
A1, | 1 | Adafruit_Feather_M0_Adalogger | Adafruit_Feather_M0_Adalogger | Module:Adafruit_Feather | Microcontroller module with SAMD21 Cortex-M0 MCU and SD card reader
C1, C4, C8, C12, C14, C17, | 6 | 10u | C | Capacitor_SMD:C_0805_2012Metric | Unpolarized capacitor
C2, C5, C15, | 3 | 1u | C | Capacitor_SMD:C_0805_2012Metric | Unpolarized capacitor
C3, C6, C7, C9, C10, C11, C13, C16, C18, | 9 | 0.1u | C | Capacitor_SMD:C_0805_2012Metric | Unpolarized capacitor
Cbs1, | 1 | 10u | C | Capacitor_THT:CP_Radial_D8.0mm_P3.50mm | Unpolarized capacitor
Cbuck1, | 1 | 200u | C_Polarized | Capacitor_THT:CP_Radial_D12.5mm_P5.00mm | Polarized capacitor
Cc1, | 1 | 470n | C | Capacitor_SMD:C_0805_2012Metric | Unpolarized capacitor
Cc2, | 1 | 33n | C | Capacitor_SMD:C_0805_2012Metric | Unpolarized capacitor
Cinput1, | 1 | 10u | C_Polarized | Capacitor_THT:CP_Radial_D6.3mm_P2.50mm | Polarized capacitor
Ct1, | 1 | 2.2n | C | Capacitor_SMD:C_0805_2012Metric | Unpolarized capacitor
D1, D2, D3, D4, D5, D6, | 6 | 1N5402 | 1N5402 | small_wind_turbine:TO-277A | 200V 3A General Purpose Rectifier Diode, DO-201AD
D7, D8, D9, D10, D11, D12, | 6 | LED | LED | LED_SMD:LED_0603_1608Metric | Light emitting diode
D13, | 1 | 1N5402 | 1N5402 | small_wind_turbine:SOD-323-EP_custom | 200V 3A General Purpose Rectifier Diode, DO-201AD
Dbs1, | 1 | 1N4006 | 1N4006 | small_wind_turbine:TO-277A | 800V 1A General Purpose Rectifier Diode, DO-41
Dbuck1, | 1 | 1N4006 | 1N4006 | small_wind_turbine:TO-277A | 800V 1A General Purpose Rectifier Diode, DO-41
F1, | 1 | 1.5A | Fuse | small_wind_turbine:FUSE_4527 | Fuse
J1, J2, J3, J4, | 4 | Conn_01x03_Male | Conn_01x03_Male | Connector_PinHeader_2.54mm:PinHeader_1x03_P2.54mm_Vertical | Generic connector, single row, 01x03, script generated (kicad-library-utils/schlib/autogen/connector/)
Jbat1, | 1 | Screw_Terminal_01x02 | Screw_Terminal_01x02 | small_wind_turbine:CUI_TBP01R1-508-02BE | Generic screw terminal, single row, 01x02, script generated (kicad-library-utils/schlib/autogen/connector/)
Jfuse1, | 1 | Screw_Terminal_01x03 | Screw_Terminal_01x03 | small_wind_turbine:CUI_TBP01R1-508-03BE_no_extra | Generic screw terminal, single row, 01x03, script generated (kicad-library-utils/schlib/autogen/connector/)
Jgen1, | 1 | Screw_Terminal_01x03 | Screw_Terminal_01x03 | small_wind_turbine:CUI_TBP01R1-508-03BE | Generic screw terminal, single row, 01x03, script generated (kicad-library-utils/schlib/autogen/connector/)
Jres1, | 1 | Screw_Terminal_01x02 | Screw_Terminal_01x02 | small_wind_turbine:CUI_TBP01R1-508-02BE | Generic screw terminal, single row, 01x02, script generated (kicad-library-utils/schlib/autogen/connector/)
K1, | 1 | G5LE-1 | G5LE-1 | small_wind_turbine:Relay_SPDT_Omron_G5LE-1 | Omron G5LE relay, Miniature Single Pole, SPDT, 10A
Lbuck1, | 1 | 330u | L | small_wind_turbine:smd_inductor | Inductor
Q1, | 1 | Q_NMOS_GSD | Q_NMOS_GSD | Package_TO_SOT_SMD:SOT-23 | N-MOSFET transistor, gate/source/drain
Qbuck1, | 1 | IRF6710S2 | Q_NMOS_GSD | Package_TO_SOT_THT:TO-220-3_Vertical | N-MOSFET transistor, gate/source/drain
R1, R10, R11, R18, | 4 | 4.7k | R | Resistor_SMD:R_0805_2012Metric | Resistor
R2, | 1 | 12k | R | Resistor_SMD:R_0805_2012Metric | Resistor
R3, | 1 | 3k | R | Resistor_SMD:R_0805_2012Metric | Resistor
R4, | 1 | 82k | R | Resistor_SMD:R_0805_2012Metric | Resistor
R5, | 1 | 13k | R | Resistor_SMD:R_0805_2012Metric | Resistor
R6, R9, | 2 | 200 | R | Resistor_SMD:R_0805_2012Metric | Resistor
R7, R8, | 2 | 1k | R | Resistor_SMD:R_0805_2012Metric | Resistor
R12, | 1 | 10 | R | Resistor_SMD:R_0805_2012Metric | Resistor
R13, | 1 | 300 | R | Resistor_SMD:R_0805_2012Metric | Resistor
R14, R15, R16, R17, | 4 | 130 | R | Resistor_SMD:R_0805_2012Metric | Resistor
Rc1, | 1 | 255 | R | Resistor_SMD:R_0805_2012Metric | Resistor
Rf1, | 1 | 1.27k | R | Resistor_SMD:R_0805_2012Metric | Resistor
Rsh1, Rsh2, | 2 | 10m | R | Resistor_SMD:R_1206_3216Metric | Resistor
Rt1, | 1 | 7.87k | R | Resistor_SMD:R_0805_2012Metric | Resistor
SW1, | 1 | SW_Push_SPDT | SW_Push_SPDT | small_wind_turbine:manual_switch | Momentary Switch, single pole double throw
TP1, TP2, TP3, TP4, TP6, TP8, TP9, TP10, TP11, | 9 | TestPoint_2Pole | TestPoint_2Pole | small_wind_turbine:Oscilloscope_Test_Point | 2-polar test point
U2, | 1 | UC2844A | UC2844A | Package_SO:SOIC-8_3.9x4.9mm_P1.27mm
U3, | 1 | LTC4440ES6 | LTC4440ES6 | Package_TO_SOT_SMD:SOT-23-6 | High-side, N-Channel, Mosfet driver, 80V input, -40Â°C to +85Â°C, SOT23-6
U4, | 1 | Opamp_Quad | Opamp_Quad | Package_SO:SOIC-14_3.9x8.7mm_P1.27mm | Quad operational amplifier
U5, U6, | 2 | INA240A1D | INA240A1D | Package_SO:SOIC-8_3.9x4.9mm_P1.27mm | High- and Low-Side, Bidirectional, Zero-Drift, Current-Sense Amplifier With Enhanced PWM Rejection, 20V/V, SOIC-8
U7, U8, | 2 | MCP3021 | MCP3021 | Package_TO_SOT_SMD:SOT-23-5
U9, | 1 | MCP4725xxx-xCH | MCP4725xxx-xCH | Package_TO_SOT_SMD:SOT-23-6 | 12-bit Digital-to-Analog Converter, integrated EEPROM, I2C interface, SOT-23-6
U10, | 1 | AZ1117-5.0 | AZ1117-5.0 | Package_TO_SOT_SMD:SOT-223-3_TabPin2 | 1A 20V Fixed LDO Linear Regulator, 5.0V, SOT-89/SOT-223/TO-220/TO-252/TO-263

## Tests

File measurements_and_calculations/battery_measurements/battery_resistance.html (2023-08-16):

# Battery Internal Resistance¶

Author: Ian Eykamp, Date: June 20, 2023

### Goals¶

To calculate the internal resistance of the 12V marine batteries in our posession in the lab. The link to purchase them is here (https://www.westmarine.com/west-marine-group-24-dual-purpose-agm-battery-79-amp-hours-15020233.html), and I have not found the datasheet for the batteries yet, with a curve of voltage vs. state of charge (SOC).

### Methodology¶

A battery's internal resistance manifests as a small resistance in series with the load. When we measure the battery terminals without anything between them (unloaded case), we get the true voltage of the battery. When we add a load resistor between the terminals, we get a voltage divider consisting of the load resistor and the internal resistance. The voltage across the load resistor $R_2$ is given by $V_{loaded} = V_{unloaded} \cdot \frac{R_2}{(R_{internal} + R_2)}$.

Thus, the internal resistance can be calculated by $(R_{internal} + R_2) = \frac{V_{unloaded}}{V_{loaded}} \cdot R_2$,

$R_{internal} = \frac{V_{unloaded}}{V_{loaded}} \cdot R_2 - R_2 = (\frac{V_{unloaded}}{V_{loaded}} - 1) \cdot R_2$.

I connected a 100Ω and a 6.8Ω 5W resistor across the terminals of all three batteries that we have in the lab. The internal resistances for each test are shown below.

In [ ]:

import numpy as np
import pandas as pd
from pint import UnitRegistry

# use pint
units = UnitRegistry()
units.default_format = "~P.2f"

In [ ]:

def calculate_R1(Vin, Vout, R2):
    R1 = R2 * (Vin / Vout - 1)
    return R1

# testing 3 batteries
unloaded = np.array([12.55, 12.62, 12.86])
loaded_100Ohm = np.array([12.54, 12.57, 12.85])
loaded_6_8Ohm = np.array([12.24, 11.99, 12.60])

print(f"Calculated internal resistance using a 100Ω resistor: {calculate_R1(unloaded, loaded_100Ohm, 100)}")
print(f"Calculated internal resistance using a 6.8Ω resistor: {calculate_R1(unloaded, loaded_6_8Ohm, 6.8)}")

Calculated internal resistance using a 100Ω resistor: [0.07974482 0.39777247 0.07782101]
Calculated internal resistance using a 6.8Ω resistor: [0.17222222 0.35729775 0.14031746]

Using a smaller load resistance yields more precise measurements. The 100Ω and 6.8Ω resistors gave similar orders of magnitude.

The internal resistance of the first and last batteries is on the order of 100mΩ. This is a typical value for a battery's internal resistance. The middle battery has an abnormally high internal resistance appraoching 400mΩ. This might be a sign that the middle battery is older or damaged.

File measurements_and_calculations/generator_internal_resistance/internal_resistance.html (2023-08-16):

# Generator Internal Resistance Calculations¶

Author: Ian Eykamp, Date: 6/16/2023

## Purpose¶

All generators have some amount of internal resistance, which allows there to be a variable voltage drop across the terminals, even if the generator always outputs the same emf. By connecting various resistors across the terminals (using no resistance as a baseline), I can figure out what the internal resistance is.

### Import libraries¶

plecs_helper.py is a file I created which defines some helper functions for nice plots and getting data off the oscilloscope and out of PLECS.

In [ ]:

import numpy as np
import pandas as pd
import matplotlib.pyplot as plt
import matplotlib.ticker as mtick
from UliEngineering.EngineerIO import format_value
from si_prefix import si_format
import plecs_helper as helper
%matplotlib
%matplotlib inline

# Imports and setup
from pint import UnitRegistry, Quantity
from scipy.signal import find_peaks
from scipy.optimize import fsolve

# pandas display using scientific notation
# pd.set_option('display.float_format', lambda x: f'{x:.3e}')

# use pint
units = UnitRegistry()
units.default_format = "~P.2f"

def to_decibels(arr, dc_gain = 0):
    return np.log10(np.abs(arr)) * 20 + dc_gain

Using matplotlib backend: <object object at 0x0000029CAE9AC580>

C:\Users\ieykamp\AppData\Local\Packages\PythonSoftwareFoundation.Python.3.9_qbz5n2kfra8p0\LocalCache\local-packages\Python39\site-packages\scipy\__init__.py:146: UserWarning: A NumPy version >=1.16.5 and <1.23.0 is required for this version of SciPy (detected version 1.23.1
  warnings.warn(f"A NumPy version >={np_minversion} and <{np_maxversion}"

### Import Data¶

I connected the oscilloscope leads between two terminals of the generator (the third terminal was left dangling). I set the oscilloscope up with 2V/division (y axis) and 5s/division (time axis). That way, I got a trace which lasted more than 30 seconds, enough for it to slow down considerably. I used the data density setting of 12k data points, and this was easily able to capture all the peaks. I spun the turbine by hand by giving it a moderate shove. It started spinning with a frequency around 6Hz, and as it slowed down, I was able to capture its frequency and amplitude on the oscilloscope.

I captured one dataset with no load, and three further datasets at 100Ohm, 6.8Ohm, and (6.8 || (6.8 + 6.8)) Ohm loads between the terminals I was measuring.

In [ ]:

# Import data
(df_1, tspan, tstep) = helper.read_rigol_csv("oscilloscope_data/unloaded.csv", ch1 = "unloaded")
(df_2, tspan, tstep) = helper.read_rigol_csv("oscilloscope_data/100Ohm.csv", ch1 = "100Ohm")
(df_3, tspan, tstep) = helper.read_rigol_csv("oscilloscope_data/6_8Ohm.csv", ch1 = "6.8Ohm")
(df_4, tspan, tstep) = helper.read_rigol_csv("oscilloscope_data/4_5Ohm.csv", ch1 = "4.5Ohm")

# Combine all variables into one for convenience
df = df_1.set_index("t").join([df_2.set_index("t"), df_3.set_index("t"), df_4.set_index("t")]).reset_index()
# print(df.head(20))

### Plot Data¶

I calculated the frequency by looking at the spacing of the peaks. After smoothing out the frequency and the peak values, I found the location where each trace crossed 4Hz and took the amplitude at that location. Since the amplitude depends on frequency, this is to normalize across datasets, since the turbine is not necsessarily spinning at the same frequency at the same timestamp.

In [ ]:

def moving_average(x, w):
    w = int(w / 2) * 2
    convolution = np.convolve(x, np.ones(w), 'full') / w
    return convolution[int(w/2):-int(w/2)+1]

def find_y_crossing_monotonic_decrease(y_vals, y_target):
    left_side_idx = list(np.arange(len(y_vals))[y_vals > y_target])
    return left_side_idx[-1]

def interpolate_outliers(y_vals, outlier_bool):
    outlier_idx = np.nonzero(outlier_bool)[0]
    if len(outlier_idx) == 0:
        return y_vals
    assert(all(np.diff(outlier_idx) > 1))
    assert(all(outlier_idx > 0) and all(outlier_idx < len(y_vals - 1))) # not the first or last element
    for idx in outlier_idx:
        y_vals[idx] = (y_vals[idx - 1] + y_vals[idx + 1]) / 2
    return y_vals

df_zoom = df[(df["t"] > 3) & (df["t"] < 25)]
fig, ((ax1, ax2), (ax3, ax4)) = plt.subplots(nrows = 2, ncols = 2, sharex = True, sharey = True, figsize = (16, 12))
fig.autofmt_xdate()

ax_list = [ax1, ax2, ax3, ax4]
channel_list = ["unloaded", "100Ohm", "6.8Ohm", "4.5Ohm"]
label_list = ["Unloaded", "100Ohm Load", "6.8Ohm Load", "4.5Ohm Load"]

amplitudes = []
for (ax, channel, label) in zip(ax_list, channel_list, label_list):
    helper.axes_labels("Oscilloscope timestamp", "s", "Voltage", "V", title = label, ax = ax)

    ax.plot(df_zoom["t"], df_zoom[channel], label = label)

    # find peaks for frequency and envelope amplitude analysis
    peak_idx = find_peaks(df_zoom[channel], distance = 25, width = 25)[0]
    df_peak_trace = df_zoom.iloc[peak_idx]
    smooth_peaks = moving_average(df_peak_trace[channel], 10)

    # find frequency using time difference between peaks
    frequency = np.hstack((0, 1 / (np.diff(df_peak_trace["t"]))))
    smooth_frequency = moving_average(interpolate_outliers(frequency, frequency > 20), 10)
    
    # find the envelope amplitude at a certain frequency for normalized comparison between datasets
    target_freq = 4 # Hz
    target_freq_idx = find_y_crossing_monotonic_decrease(y_vals = smooth_frequency, y_target = target_freq)
    amplitude_at_target_freq = smooth_peaks[target_freq_idx]
    amplitudes.append(amplitude_at_target_freq)

    # plot peaks
    ax.scatter(df_peak_trace["t"], df_peak_trace[channel])
    ax.plot(df_peak_trace["t"], smooth_peaks, linestyle = "dashed", color = "green")
    ax.legend(loc = "upper right")
    
    # plot frequency
    rax = ax.twinx()
    helper.axes_labels("Oscilloscope timestamp", "s", "Frequency", "Hz", title = label, ax = rax)
    rax.plot(df_peak_trace["t"], smooth_frequency, color = "orange", label = "Frequency (Hz)")
    rax.set_ylim(0, 6.9)
    rax.legend(loc = "lower right")

C:\Users\ieykamp\AppData\Local\Temp\ipykernel_13580\1153253338.py:36: PeakPropertyWarning: some peaks have a width of 0
  peak_idx = find_peaks(df_zoom[channel], distance = 25, width = 25)[0]
C:\Users\ieykamp\AppData\Local\Temp\ipykernel_13580\1153253338.py:36: PeakPropertyWarning: some peaks have a width of 0
  peak_idx = find_peaks(df_zoom[channel], distance = 25, width = 25)[0]
C:\Users\ieykamp\AppData\Local\Temp\ipykernel_13580\1153253338.py:36: PeakPropertyWarning: some peaks have a width of 0
  peak_idx = find_peaks(df_zoom[channel], distance = 25, width = 25)[0]

The abrupt drop off in frequency near the end is a figment of the smoothing algorithm and can be ignored.

The amplitudes at 4Hz are as follows. I calcualted the internal resistance $R_1$ using the following equation, based on the load resistor I was using: $R1 = R2 \cdot (\frac{V_{in}}{V_{out}} - 1)$, where $V_{in}$ is the unloaded amplitude and $V_{out}$ is the amplitude given a load resistor of $R_2$. The internal resistance of the generator is approximately $14.5 \Omega \pm 1 \Omega$.

In [ ]:

def calculate_R1(Vin, Vout, R2):
    R1 = R2 * (Vin / Vout - 1)
    return R1

print("Amplitude with no load at 4Hz =", np.round(amplitudes[0], 3) * units.volt)
print("Amplitude with 100Ω load at 4Hz =", np.round(amplitudes[1], 3) * units.volt)
print("Amplitude with 6.8Ω load at 4Hz =", np.round(amplitudes[2], 3) * units.volt)
print("Amplitude with 4.5Ω load at 4Hz =", np.round(amplitudes[3], 3) * units.volt)
print("")

print("Three different calculations for internal resistance:")
R1_100Ohm_test = calculate_R1(amplitudes[0] * units.volt, amplitudes[1] * units.volt, 100 * units.ohm)
print(f"R1 = {R1_100Ohm_test}")
R1_6_8Ohm_test = calculate_R1(amplitudes[0] * units.volt, amplitudes[2] * units.volt, 6.8 * units.ohm)
print(f"R1 = {R1_6_8Ohm_test}")
R1_4_5Ohm_test = calculate_R1(amplitudes[0] * units.volt, amplitudes[3] * units.volt, 1/(1/6.8 + 1/(2 * 6.8)) * units.ohm)
print(f"R1 = {R1_4_5Ohm_test}")

R1 = np.mean(Quantity.from_list([R1_100Ohm_test, R1_6_8Ohm_test, R1_4_5Ohm_test]))
print(f"Average R1 = {np.round(R1, 2)}")

Amplitude with no load at 4Hz = 1.17 V
Amplitude with 100Ω load at 4Hz = 1.02 V
Amplitude with 6.8Ω load at 4Hz = 0.38 V
Amplitude with 4.5Ω load at 4Hz = 0.26 V

Three different calculations for internal resistance:
R1 = 13.97 Ω
R1 = 14.17 Ω
R1 = 15.93 Ω
Average R1 = 14.69 ohm

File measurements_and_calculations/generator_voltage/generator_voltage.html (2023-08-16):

# Small Turbine Generator Voltage (Wind Powered)¶

Author: Ian Eykamp, Date: 6/16/2023

## Purpose¶

I powered the wind turbine using the wind tunnel in the 4th floor Rocketry lab. I measured the frequency and magnitude of the voltage generated at different wind speeds. I repeated calculations used to find the internal resistance of the generator.

The wind tunnel has a power setting from 0-80 that corresponds to how fast (in Hz) the fan inside the wind tunnel is spinning. So it doesn't really correlate with an actual wind speed felt by the turbine. There is a table that correlates the speed setting to wind speed, but this means wind speed inside the tunnel, which is different and much lower at the outlet, especially as it diffuses into the open space. The first set of measurements is taken at a setting of 20 out of 80; for the later measurements, I set it to either 30 or 39 out of 80, because that was as fast as I felt comfortable letting the wind turbine spin safely.

### Import libraries¶

plecs_helper.py is a file I created which defines some helper functions for nice plots and getting data off the oscilloscope and out of PLECS.

In [ ]:

import numpy as np
import pandas as pd
import matplotlib.pyplot as plt
import matplotlib.ticker as mtick
from UliEngineering.EngineerIO import format_value
from si_prefix import si_format
import plecs_helper as helper
%matplotlib
%matplotlib inline

# Imports and setup
from pint import UnitRegistry
from scipy.signal import find_peaks
from scipy.optimize import fsolve

import warnings
warnings.filterwarnings("ignore", message="some peaks have a width of 0") # get rid of an annoying warning printout

# pandas display using scientific notation
# pd.set_option('display.float_format', lambda x: f'{x:.3e}')

# use pint
units = UnitRegistry()
units.default_format = "~P.2f"

def to_decibels(arr, dc_gain = 0):
    return np.log10(np.abs(arr)) * 20 + dc_gain

def generator_hz_to_rpm(hz):
    # the generator probably has multiple poles, which means it will exhibit one full period of the sine wave
    # while only making 1 / n_poles of a rotation.
    n_poles = 3 # I don't know whether n_poles = 2 or 3
    return hz * 60 / n_poles

Using matplotlib backend: TkAgg

## Experiment 1: With respect to load resistance¶

I connected the oscilloscope leads between two terminals of the generator (the third terminal was left dangling).

I captured one dataset with no load, and three further datasets at 100Ohm, 6.8Ohm, and (6.8 || (6.8 + 6.8)) Ohm loads between the terminals I was measuring. I did not write it down, and sadly, I don't know what wind speed setting the wind tunnel was operating at. My best guess is a fan speed of 20Hz.

The peak voltage $V_{peak}$ available from the 3-phase generator is equal to the greatest instantaneous difference between any two phases. Here, it is the maximum peak-to-trough voltage. This is two times the amplitude of the wave. The RMS voltage for the 3-phase generator is $V_{RMS} = \frac{V_{peak}}{\sqrt{3}}$. I calculated the frequency by looking at the spacing of the peaks.

In [ ]:

# Import data
# (df_1, tspan, tstep) = helper.read_rigol_csv("oscilloscope_data/Newfile1.csv", ch1 = "6.8Ohm_Delta")
(df_1, tspan, tstep) = helper.read_rigol_csv("oscilloscope_data/Newfile2.csv", ch1 = "4.5Ohm") # ch1 = "4.5Ohm")
(df_2, tspan, tstep) = helper.read_rigol_csv("oscilloscope_data/Newfile3.csv", ch1 = "100Ohm") # ch1 = "100Ohm")
(df_3, tspan, tstep) = helper.read_rigol_csv("oscilloscope_data/Newfile4.csv", ch1 = "6.8Ohm") # ch1 = "6.8Ohm")
(df_4, tspan, tstep) = helper.read_rigol_csv("oscilloscope_data/Newfile5.csv", ch1 = "unloaded") # ch1 = "unloaded")
# (df_6, tspan, tstep) = helper.read_rigol_csv("oscilloscope_data/Newfile6.csv", ch1 = "100Ohm_30Hz")

# Combine all variables into one for convenience
df = df_1.set_index("t").join([df_2.set_index("t"), df_3.set_index("t"), df_4.set_index("t")]).reset_index()
# print(df.head(20))

df_zoom = df[(df["t"] > 1) & (df["t"] < 6)]
fig, ((ax1, ax2), (ax3, ax4)) = plt.subplots(nrows = 2, ncols = 2, sharex = True, sharey = True, figsize = (16, 12))
fig.autofmt_xdate()

ax_list = [ax1, ax2, ax3, ax4]
channel_list = ["unloaded", "100Ohm", "6.8Ohm", "4.5Ohm"]
label_list = ["Unloaded", "100Ohm Load", "6.8Ohm Load", "4.5Ohm Load"]

frequencies = []
amplitudes = []
for (ax, channel, label) in zip(ax_list, channel_list, label_list):
    helper.axes_labels("Oscilloscope timestamp", "s", "Voltage", "V", title = label, ax = ax)

    # find peaks for frequency and envelope amplitude analysis
    peak_idx = find_peaks(df_zoom[channel], distance = 100, width = 75)[0]
    df_peak_trace = df_zoom.iloc[peak_idx]

    # find frequency using time difference between peaks
    frequency_points = np.hstack((0, 1 / (np.diff(df_peak_trace["t"]))))
    mean_freq = np.mean(frequency_points)
    frequencies.append(mean_freq)
    amplitude_points = df_peak_trace[channel]
    mean_amplitude = np.mean(amplitude_points)
    amplitudes.append(mean_amplitude)

    # print(frequencies)

    # plot data with peaks
    ax.plot(df_zoom["t"], df_zoom[channel], label = label)
    ax.scatter(df_peak_trace["t"], df_peak_trace[channel])
    ax.legend(loc = "upper right")

    print(f"With {('no load' if label == 'Unloaded' else 'a ' + label).lower()}, the generator had an amplitude of {mean_amplitude:.2f}V and a frequency of {mean_freq:.3f}Hz; hence {generator_hz_to_rpm(mean_freq):.0f} RPM")

With no load, the generator had an amplitude of 17.19V and a frequency of 5.172Hz; hence 103 RPM
With a 100ohm load, the generator had an amplitude of 14.49V and a frequency of 4.942Hz; hence 99 RPM
With a 6.8ohm load, the generator had an amplitude of 4.76V and a frequency of 4.257Hz; hence 85 RPM
With a 4.5ohm load, the generator had an amplitude of 3.38V and a frequency of 4.062Hz; hence 81 RPM

I calcualted the internal resistance $R_1$ using the following equation, based on the load resistor I was using: $R1 = R2 \cdot (\frac{V_{in}}{V_{out}} - 1)$, where $V_{in}$ is the unloaded amplitude and $V_{out}$ is the amplitude given a load resistor of $R_2$.

The input (unloaded generator) voltage is proportional to the frequency of rotation. Hence, we correct input voltage for calculation with test case $i$ by using $V_{in, i} = V_{in, 0} \cdot \frac{f_i}{f_0}$. After correcting for frequency, the calculated internal resistance values get a lot closer together.

The internal resistance of the generator is approximately $13.5 \Omega \pm 0.2 \Omega$.

In [ ]:

# always run the previous cell before re-running this cell
# otherwise, you will get bogus numbers, 
# because the subsequent cell overwrites some of the variables used here.

def calculate_R1(Vin, Vout, R2):
    R1 = R2 * (Vin / Vout - 1)
    return R1

unloaded_amplitude = amplitudes[0]
unloaded_frequency = frequencies[0]

print("Three different calculations for internal resistance:")
# print("Before correcting for frequency")
# print("R1 =", calculate_R1(unloaded_amplitude * units.volt, amplitudes[1] * units.volt, 100 * units.ohm))
# print("R1 =", calculate_R1(unloaded_amplitude * units.volt, amplitudes[2] * units.volt, 6.8 * units.ohm))
# print("R1 =", calculate_R1(unloaded_amplitude * units.volt, amplitudes[3] * units.volt, 1/(1/6.8 + 1/(2 * 6.8)) * units.ohm))
# print("")
print("After correcting for frequency")
print("R1 =", calculate_R1(unloaded_amplitude * units.volt * frequencies[1] / unloaded_frequency, amplitudes[1] * units.volt, 100 * units.ohm))
print("R1 =", calculate_R1(unloaded_amplitude * units.volt * frequencies[2] / unloaded_frequency, amplitudes[2] * units.volt, 6.8 * units.ohm))
print("R1 =", calculate_R1(unloaded_amplitude * units.volt * frequencies[3] / unloaded_frequency, amplitudes[3] * units.volt, 1/(1/6.8 + 1/(2 * 6.8)) * units.ohm))
print("")
print(f"Maximum internal power dissipation when short circuited = {((max(amplitudes) * units.volt) ** 2 / (13.5 * units.ohm)).to_compact(units.watt)}")

Three different calculations for internal resistance:
After correcting for frequency
R1 = 13.41 Ω
R1 = 13.42 Ω
R1 = 13.61 Ω

Maximum internal power dissipation when short circuited = 21.90 W

## Experiment 2: With respect to wind speed and load resistance¶

In [ ]:

# Import data
# (df_1, tspan, tstep) = helper.read_rigol_csv("oscilloscope_data/Newfile1.csv", ch1 = "6.8Ohm_Delta")
(df_1, tspan, tstep) = helper.read_rigol_csv("oscilloscope_data/high_speed/Newfile1.csv", ch1 = "100Ohm, 30Hz") # ch1 = "6.8Ohm, 39Hz")
(df_2, tspan, tstep) = helper.read_rigol_csv("oscilloscope_data/high_speed/Newfile2.csv", ch1 = "100Ohm, 39Hz") # ch1 = "100Ohm, 39Hz")
(df_3, tspan, tstep) = helper.read_rigol_csv("oscilloscope_data/high_speed/Newfile3.csv", ch1 = "6.8Ohm, 30Hz") # ch1 = "6.8Ohm, 30Hz")
(df_4, tspan, tstep) = helper.read_rigol_csv("oscilloscope_data/high_speed/Newfile4.csv", ch1 = "6.8Ohm, 39Hz") # ch1 = "100Ohm, 30Hz")
# (df_6, tspan, tstep) = helper.read_rigol_csv("oscilloscope_data/Newfile6.csv", ch1 = "100Ohm_30Hz")

# Combine all variables into one for convenience
df = df_1.set_index("t").join([df_2.set_index("t"), df_3.set_index("t"), df_4.set_index("t")]).reset_index()
# print(df.head(20))

df_zoom = df[(df["t"] > 1) & (df["t"] < 6)]
fig, ((ax1, ax2), (ax3, ax4)) = plt.subplots(nrows = 2, ncols = 2, sharex = True, sharey = True, figsize = (16, 12))
fig.autofmt_xdate()

ax_list = [ax1, ax2, ax3, ax4]
channel_list = ["100Ohm, 30Hz", "100Ohm, 39Hz", "6.8Ohm, 30Hz", "6.8Ohm, 39Hz"]
label_list = ["100Ohm, 30Hz", "100Ohm, 39Hz", "6.8Ohm, 30Hz", "6.8Ohm, 39Hz"]

frequencies = []
amplitudes = []
for (ax, channel, label) in zip(ax_list, channel_list, label_list):
    helper.axes_labels("Oscilloscope timestamp", "s", "Voltage", "V", title = label, ax = ax)

    # find peaks for frequency and envelope amplitude analysis
    peak_idx = find_peaks(df_zoom[channel], distance = 50, width = 50)[0]
    df_peak_trace = df_zoom.iloc[peak_idx]

    # find frequency using time difference between peaks
    frequency_points = np.hstack((0, 1 / (np.diff(df_peak_trace["t"]))))
    mean_freq = np.mean(frequency_points)
    frequencies.append(mean_freq)
    amplitude_points = df_peak_trace[channel]
    mean_amplitude = np.mean(amplitude_points)
    amplitudes.append(mean_amplitude)

    # print(frequencies)

    # plot data with peaks
    ax.plot(df_zoom["t"], df_zoom[channel], label = label)
    ax.scatter(df_peak_trace["t"], df_peak_trace[channel])
    ax.legend(loc = "upper right")

    print(f"At test settings of [{label}], the generator had an amplitude of {mean_amplitude:.2f}V and a frequency of {mean_freq:.3f}Hz; hence {generator_hz_to_rpm(mean_freq):.0f} RPM")

At test settings of [100Ohm, 30Hz], the generator had an amplitude of 22.79V and a frequency of 8.137Hz; hence 163 RPM
At test settings of [100Ohm, 39Hz], the generator had an amplitude of 30.19V and a frequency of 10.743Hz; hence 215 RPM
At test settings of [6.8Ohm, 30Hz], the generator had an amplitude of 7.63V and a frequency of 7.318Hz; hence 146 RPM
At test settings of [6.8Ohm, 39Hz], the generator had an amplitude of 10.71V and a frequency of 10.447Hz; hence 209 RPM

This is mostly just fun to see how much voltage we can get out of the generator at higher wind speeds. I did not feel like we could safely increase the wind speed much more before making our test stand dangerous. In the unloaded case, we can easily get 30V peak-to-center out of the generator for testing purposes.

Once again, we can repeat the internal resistance calculations and get similar values within $\pm 5\Omega$ of the previous values. Keep in mind that the internal impedance of the generator may be dependent on frequency.

In [ ]:

print("Four more calculations for internal resistance:")
# print("Before correcting for frequency")
# print("R1 =", calculate_R1(unloaded_amplitude * units.volt, amplitudes[0] * units.volt, 100 * units.ohm))
# print("R1 =", calculate_R1(unloaded_amplitude * units.volt, amplitudes[1] * units.volt, 100 * units.ohm))
# print("R1 =", calculate_R1(unloaded_amplitude * units.volt, amplitudes[2] * units.volt, 6.8 * units.ohm))
# print("R1 =", calculate_R1(unloaded_amplitude * units.volt, amplitudes[3] * units.volt, 6.8 * units.ohm))
# print("")
print("After correcting for frequency")
print("R1 =", calculate_R1(unloaded_amplitude * units.volt * frequencies[0] / unloaded_frequency, amplitudes[0] * units.volt, 100 * units.ohm))
print("R1 =", calculate_R1(unloaded_amplitude * units.volt * frequencies[1] / unloaded_frequency, amplitudes[1] * units.volt, 100 * units.ohm))
print("R1 =", calculate_R1(unloaded_amplitude * units.volt * frequencies[2] / unloaded_frequency, amplitudes[2] * units.volt, 6.8 * units.ohm))
print("R1 =", calculate_R1(unloaded_amplitude * units.volt * frequencies[3] / unloaded_frequency, amplitudes[3] * units.volt, 6.8 * units.ohm))
print("")
print(f"Maximum internal power dissipation when short circuited = {((max(amplitudes) * units.volt) ** 2 / (13.5 * units.ohm)).to_compact(units.watt)}")

Four more calculations for internal resistance:
After correcting for frequency
R1 = 18.69 Ω
R1 = 18.31 Ω
R1 = 14.88 Ω
R1 = 15.25 Ω

Maximum internal power dissipation when short circuited = 67.50 W

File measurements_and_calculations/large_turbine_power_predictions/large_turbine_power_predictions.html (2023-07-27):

# Large Turbine Wind Speed and Power Predictions¶

Author: Ian Eykamp, Date: July 27, 2023

## Purpose¶

To give an estimate of the voltage and power that will be generated by the large wind turbine during operation on Olin's campus. This will be useful for speccing a dump load resistor, which is done at the end of this document.

## Assumptions¶

In this exploration, I used several secondary sources that all refer (I think) to the specific model of turbine and generator that we have at Olin. One (https://olincollege-my.sharepoint.com/personal/dmerzenich_olin_edu/_layouts/15/onedrive.aspx) is a write-up of a similar installation by Eastern Wind Power on top of a building, along with modeled vs. measured power outputs. It is an assumption that those measurements will be valid at Olin at the same wind speed levels. The average wind speed at Olin is much lower, which might mean the bulk of the data gathered at that site is not relevant.

Another secondary source is the PLECS model for the "1FW3208-1EE" generator supplied with a constant speed of rotation (in rpm). This model was provided by Supa as part of several other PLECS models attemting to answer a similar question. I have no way to confirm the accuracy of that model.

Despite these caveats, a sign that I am in the right ballpark is that the results from all of the data I chose to analyze do approximately line up. Moreover, my final recommendation of a 12m/s cut-out wind speed is both in the ballpark of other recommendations and is a more conservative number than all other estimates. In this case, it does not hurt to be conservative, because even at 12m/s, it is very rare that we will ever reach the cut-out wind speed on Olin's campus since our wind speeds are very low on average.

## Import Libraries¶

In [ ]:

import numpy as np
import pandas as pd
import matplotlib.pyplot as plt
import matplotlib.ticker as mtick
from UliEngineering.EngineerIO import format_value
from si_prefix import si_format
import plecs_helper as helper
%matplotlib
%matplotlib inline

# Imports and setup
from pint import UnitRegistry

# pandas display using scientific notation
# pd.set_option('display.float_format', lambda x: f'{x:.3e}')

# use pint
units = UnitRegistry()
units.default_format = "~P.2f"

Using matplotlib backend: <object object at 0x000002A0B74EB4E0>

## Secondary Sources For Power vs. Wind Speed¶

### Dylan and Anna's OneDrive¶

Dylan Merzenich and Anna Letcher Hartman worked on the mechanical side of the turbine, designing a 6-foot tower for the turbine to sit on. Their work is consolidated here (https://olincollege-my.sharepoint.com/personal/dmerzenich_olin_edu/_layouts/15/onedrive.aspx) (you will need OneDrive permission).

On page 3 of this document (https://olincollege-my.sharepoint.com/personal/dmerzenich_olin_edu/_layouts/15/onedrive.aspx?ga=1), there is a table linking wind speed to generator revolutions per minute. This is tabulated using Pandas in the script below.

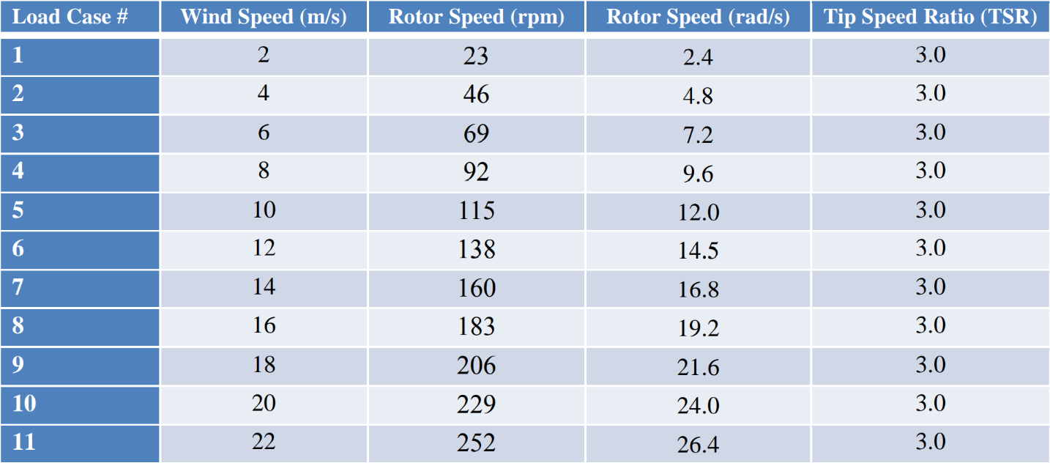
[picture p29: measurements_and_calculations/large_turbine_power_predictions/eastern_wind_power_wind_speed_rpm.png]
Eastern Wind Power wind speed vs. generator revolutions per minute table


In [ ]:

df_rotor_speed = pd.DataFrame(
    columns = ["Load Case #", "Wind Speed (m/s)", "Rotor Speed (rpm)", "Rotor Speed (rad/s)", "Tip Speed Ratio (TSR)"], 
    data = [
        [1,  2,  23,  2.4,  3.0],
        [2,  4,  46,  4.8,  3.0],
        [3,  6,  69,  7.2,  3.0],
        [4,  8,  92,  9.6,  3.0],
        [5,  10, 115, 12.0, 3.0],
        [6,  12, 138, 14.5, 3.0],
        [7,  14, 160, 16.8, 3.0],
        [8,  16, 183, 19.2, 3.0],
        [9,  18, 206, 21.6, 3.0],
        [10, 20, 229, 24.0, 3.0],
        [11, 22, 252, 26.4, 3.0],
    ]
).set_index("Load Case #")
print(df_rotor_speed)

             Wind Speed (m/s)  Rotor Speed (rpm)  Rotor Speed (rad/s)  \
Load Case #                                                             
1                           2                 23                  2.4   
2                           4                 46                  4.8   
3                           6                 69                  7.2   
4                           8                 92                  9.6   
5                          10                115                 12.0   
6                          12                138                 14.5   
7                          14                160                 16.8   
8                          16                183                 19.2   
9                          18                206                 21.6   
10                         20                229                 24.0   
11                         22                252                 26.4   

             Tip Speed Ratio (TSR)  
Load Case #                         
1                              3.0  
2                              3.0  
3                              3.0  
4                              3.0  
5                              3.0  
6                              3.0  
7                              3.0  
8                              3.0  
9                              3.0  
10                             3.0  
11                             3.0

Page 13 of ths document (https://olincollege-my.sharepoint.com/personal/dmerzenich_olin_edu/_layouts/15/onedrive.aspx?ga=1) has a graph of theoretical power output vs. wind speed based on a model used by Eastern Wind Power. It shows much higher power generation than any other source, so it can probably be used as an upper bound. It shows a cut-in wind speed of 2m/s and a cut-out at 18m/s, after which the rotor is shut down. If you extrapolate past the cut-out point, you would reach around 55kW at 20m/s, or 25kW at 15m/s.

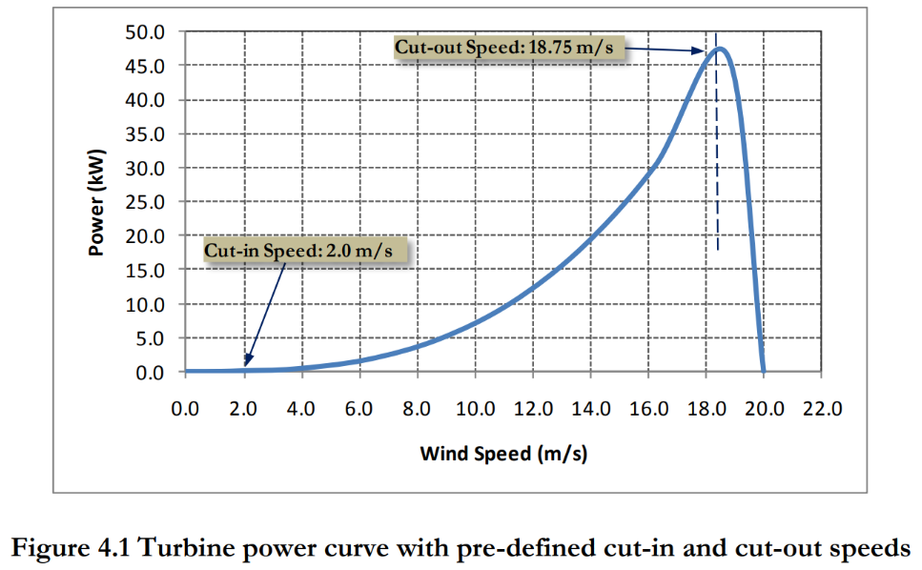
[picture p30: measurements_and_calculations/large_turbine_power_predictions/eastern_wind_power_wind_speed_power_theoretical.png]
Eastern Wind Power wind speed vs. generator power (theoretical)


I tabulated the data for use in this script by reading off the graph.

In [ ]:

df_EWP_modeled = pd.DataFrame(
    columns = ["Wind Speed (m/s)", "Power Output (kW)"], 
    data = [
        [1,  0.00],
        [2,  0.00],
        [3,  0.00],
        [4,  0.5],
        [5,  1.5],
        [6,  2.1],
        [7,  2.7],
        [8,  4],
        [9,  5.6],
        [10, 7.4],
        [11, 9.8],
        [12, 12.3],
        [13, 15.5],
        [14, 19],
        [15, 23.8],
        [16, 28.2],
        [17, 37.4],
        [18, 45.8],
        [19, 42],
        [20, 55],
    ]
)
print(df_EWP_modeled)

    Wind Speed (m/s)  Power Output (kW)
0                  1                0.0
1                  2                0.0
2                  3                0.0
3                  4                0.5
4                  5                1.5
5                  6                2.1
6                  7                2.7
7                  8                4.0
8                  9                5.6
9                 10                7.4
10                11                9.8
11                12               12.3
12                13               15.5
13                14               19.0
14                15               23.8
15                16               28.2
16                17               37.4
17                18               45.8
18                19               42.0
19                20               55.0

Page 15 of the same document (https://olincollege-my.sharepoint.com/personal/dmerzenich_olin_edu/_layouts/15/onedrive.aspx?ga=1) has a graph of the power output vs. wind speed that they actually measured. They have a cut-in point at 4m/s. Notably, they have a cut-out point at around 13m/s, at which point the rotor is controlled so that it doesn't spin any faster. At around 20m/s wind speed, the rotor is shut down completely.

I had access to an extended version of the same document as a hard copy (accessed from the Eastern Wind Power binders in Chhavi's lab), and it contains tabulted data from the graph, which is reproduced below.

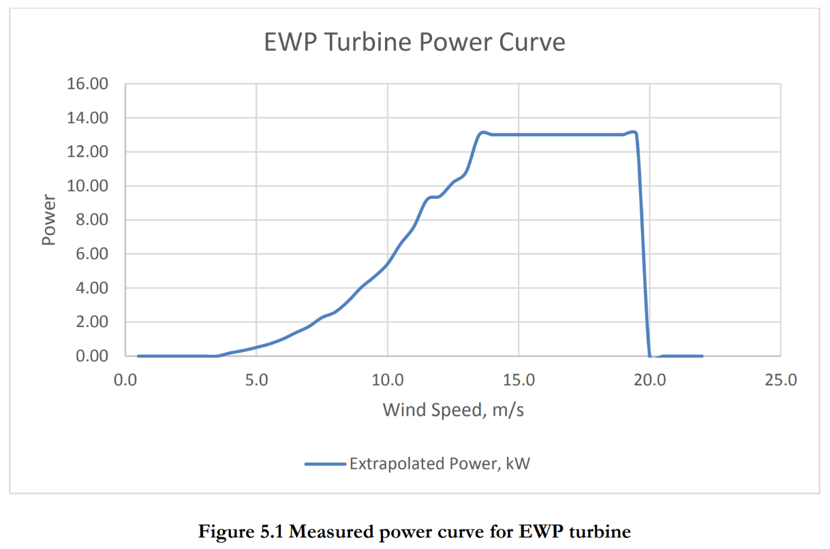
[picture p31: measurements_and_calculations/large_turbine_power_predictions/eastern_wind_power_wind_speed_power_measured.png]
Eastern Wind Power wind speed vs. generator power (measured)


In [ ]:

df_EWP_measured = pd.DataFrame(
    columns = ["Wind Speed (m/s)", "Power Output (kW)"], 
    data = [
        [0.5,  0.00],
        [1.0,  0.00],
        [1.5,  0.00],
        [2.0,  0.00],
        [2.5,  0.00],
        [3.0,  0.00],
        [3.5,  0.00],
        [4.0,  0.19],
        [4.5,  0.33],
        [5.0,  0.51],
        [5.5,  0.71],
        [6.0,  1.00],
        [6.5,  1.38],
        [7.0,  1.74],
        [7.5,  2.27],
        [8.0,  2.58],
        [8.5,  3.23],
        [9.0,  4.04],
        [9.5,  4.67],
        [10.0, 5.41],
        [10.5, 6.59],
        [11.0, 7.58],
        [11.5, 9.18],
        [12.0, 9.40],
        [12.5, 10.20],
        [13.0, 10.82],
        [13.5, 13.01],
        [14.0, 13.01],
        [14.5, 13.01],
        [15.0, 13.01],
    ]
)
print(df_EWP_measured)

    Wind Speed (m/s)  Power Output (kW)
0                0.5               0.00
1                1.0               0.00
2                1.5               0.00
3                2.0               0.00
4                2.5               0.00
5                3.0               0.00
6                3.5               0.00
7                4.0               0.19
8                4.5               0.33
9                5.0               0.51
10               5.5               0.71
11               6.0               1.00
12               6.5               1.38
13               7.0               1.74
14               7.5               2.27
15               8.0               2.58
16               8.5               3.23
17               9.0               4.04
18               9.5               4.67
19              10.0               5.41
20              10.5               6.59
21              11.0               7.58
22              11.5               9.18
23              12.0               9.40
24              12.5              10.20
25              13.0              10.82
26              13.5              13.01
27              14.0              13.01
28              14.5              13.01
29              15.0              13.01

### PLECS Model¶

I used the basic generator model connected to three resistors in a delta configuration as a dump load. The power dissipated by the dump load is dependent on the resistance and is maximized when the impedance of the load matches the internal impedance of the generator (refer to any textbook). The power dissipated is also obviously dependent on the rotor speed. I ran a basic 2-dimensional parameter sweep of the load resistance and rotor speed for $1\Omega \le R_{Load} \le 10\Omega$ and $50\text{rpm} \le \omega \le 300\text{rpm}$.

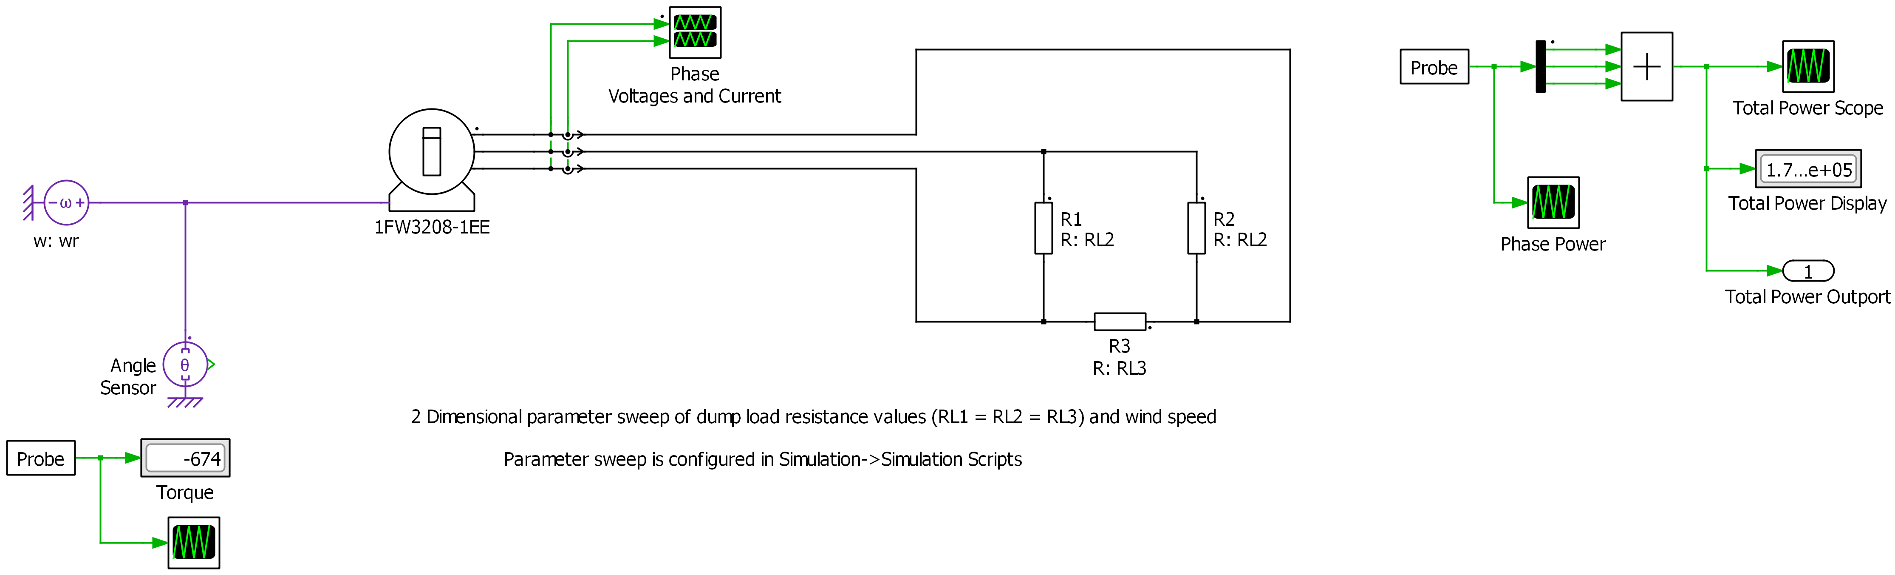
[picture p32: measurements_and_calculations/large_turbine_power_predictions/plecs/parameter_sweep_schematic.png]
Parameter Sweep PLECS Model


The script can be accessed from Simulation -> Simulation Scripts or by pressing Ctrl+Shift+T and has contents

mdl = plecs('get', '', 'CurrentCircuit');
scopepath = [mdl '/Total Power Scope'];
displaypath = [mdl '/Total Power Display'];

loadStructure = struct('RL1', 4);
loadStructure = struct('RL2', 4);
loadStructure = struct('RL3', 4);
loadStructure = struct('wr', 100);
varStructure = struct('ModelVars', loadStructure);

plecs('scope', scopepath, 'ClearTraces');

RVals = [1:10:200];
wVals = [210:50:300];

for ix = 1:length(RVals)
  varStructure.ModelVars.RL1 = RVals(ix);
  varStructure.ModelVars.RL2 = RVals(ix);
  varStructure.ModelVars.RL3 = RVals(ix);
  for jx = 1:length(wVals)
    varStructure.ModelVars.wr = wVals(jx);

    printf('\n');
    output = plecs('simulate', varStructure);
    printf('\n');

    [nrows, ncols] = size(output.Values(1,:));   % determine number of row and column in structure
    [finalValue] = output.Values(1, ncols); % % determine last value of inductor current in this run
    % Output the last value of Inductor Current in current run  
    printf('RL = %dohms, wr = %drpm, power = %dW', RVals(ix), wVals(jx), finalValue);
    plecs('scope', scopepath, 'HoldTrace', ['R = ' mat2str(RVals(ix)) ' ohms']);
  end
end

The script prints the results of the parameter sweep into the PLECS simulation console, which can be viewed from Window -> Show Console. From there, I copied all the text and pasted it into a file named plecs_parameter_sweep_3.txt. There are random printouts between each line that I don't know how to get rid of. Instead, I filter out those lines when I read the file into python.

In [ ]:

def get_params(param_str):
    resistance = float(param_str.partition("RL = ")[2].partition("ohms")[0])
    angular_velocity = float(param_str.partition("wr = ")[2].partition("rpm")[0])
    power = float(param_str.partition("power = ")[2].partition("W")[0])
    return resistance, angular_velocity, power

df_plecs = pd.DataFrame(columns = ["Resistance (ohms)", "Angular Velocity (rpm)", "Power (W)"])
with open("plecs/plecs_parameter_sweep_3.txt") as file:
    for line in file:
        if line.startswith("Kt") or line.startswith("Imax") or line.strip() == "":
            continue
        resistance, angular_velocity, power = get_params(line)
        df_plecs.loc[len(df_plecs)] = ([resistance, angular_velocity, power])

# print(df_plecs)

grouped_by_angular_velocity = df_plecs.groupby("Angular Velocity (rpm)")

fig, ax1 = plt.subplots()
helper.axes_labels("Load Resistance", "Ω", "Power Output", "W", title = "Power Output vs. Angular Velocity and Load Resistance")
for angular_velocity, group in grouped_by_angular_velocity:
    plt.plot(group["Resistance (ohms)"], group["Power (W)"], label = f"ω = {angular_velocity:.0f} rpm")
handles, labels = ax1.get_legend_handles_labels()
ax1.legend(reversed(handles), reversed(labels), title = "Angular Velocity", loc='lower right')

Out[ ]:

<matplotlib.legend.Legend at 0x2a0b8e5c340>

Lastly, I find the peak power output as well as the ideal resistance to produce it for each rotor speed (angular velocity).

In [ ]:

df_plecs_peak = pd.DataFrame(columns = ["Peak Resistance (ohms)", "Angular Velocity (rpm)", "Peak Power (W)"])

grouped_by_angular_velocity = df_plecs.groupby("Angular Velocity (rpm)")

for angular_velocity, group in grouped_by_angular_velocity:
    peak_idx = group["Power (W)"].argmax()
    peak_resistance = group["Resistance (ohms)"].iloc[peak_idx]
    peak_power = group["Power (W)"].iloc[peak_idx]
    df_plecs_peak.loc[len(df_plecs_peak)] = ([peak_resistance, angular_velocity, peak_power])

print(df_plecs_peak[["Angular Velocity (rpm)", "Peak Resistance (ohms)", "Peak Power (W)"]])

   Angular Velocity (rpm)  Peak Resistance (ohms)  Peak Power (W)
0                    50.0                     1.6         3523.79
1                   100.0                     3.2         8474.87
2                   150.0                     4.6        13542.80
3                   200.0                     6.2        18641.60
4                   250.0                     7.8        23750.70
5                   300.0                     9.2        28868.00

### Generate Tables¶

Now it's time to put all the data from these different sources together. I compare all the above datasets at several particularly relevant wind velocities. This involves linear interpolation when the exact values are not available.

In [ ]:

wind_speeds_to_tabulate = [20, 15, 12, 9, 6, 4, 2]

# this function courtesy of https://stackoverflow.com/a/51535881
def reindex_and_interpolate(df, new_index):
    return df.reindex(df.index | new_index).interpolate(method='index', limit_direction='both').loc[new_index]

df_final_rotor_speeds = reindex_and_interpolate(df_rotor_speed.set_index("Wind Speed (m/s)"), wind_speeds_to_tabulate)
# print(df_final_rotor_speeds)
df_final_plecs = reindex_and_interpolate(df_plecs_peak.set_index("Angular Velocity (rpm)"), df_final_rotor_speeds["Rotor Speed (rpm)"])
df_final_plecs["Peak Power (kW)"] = df_final_plecs["Peak Power (W)"] / 1000
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

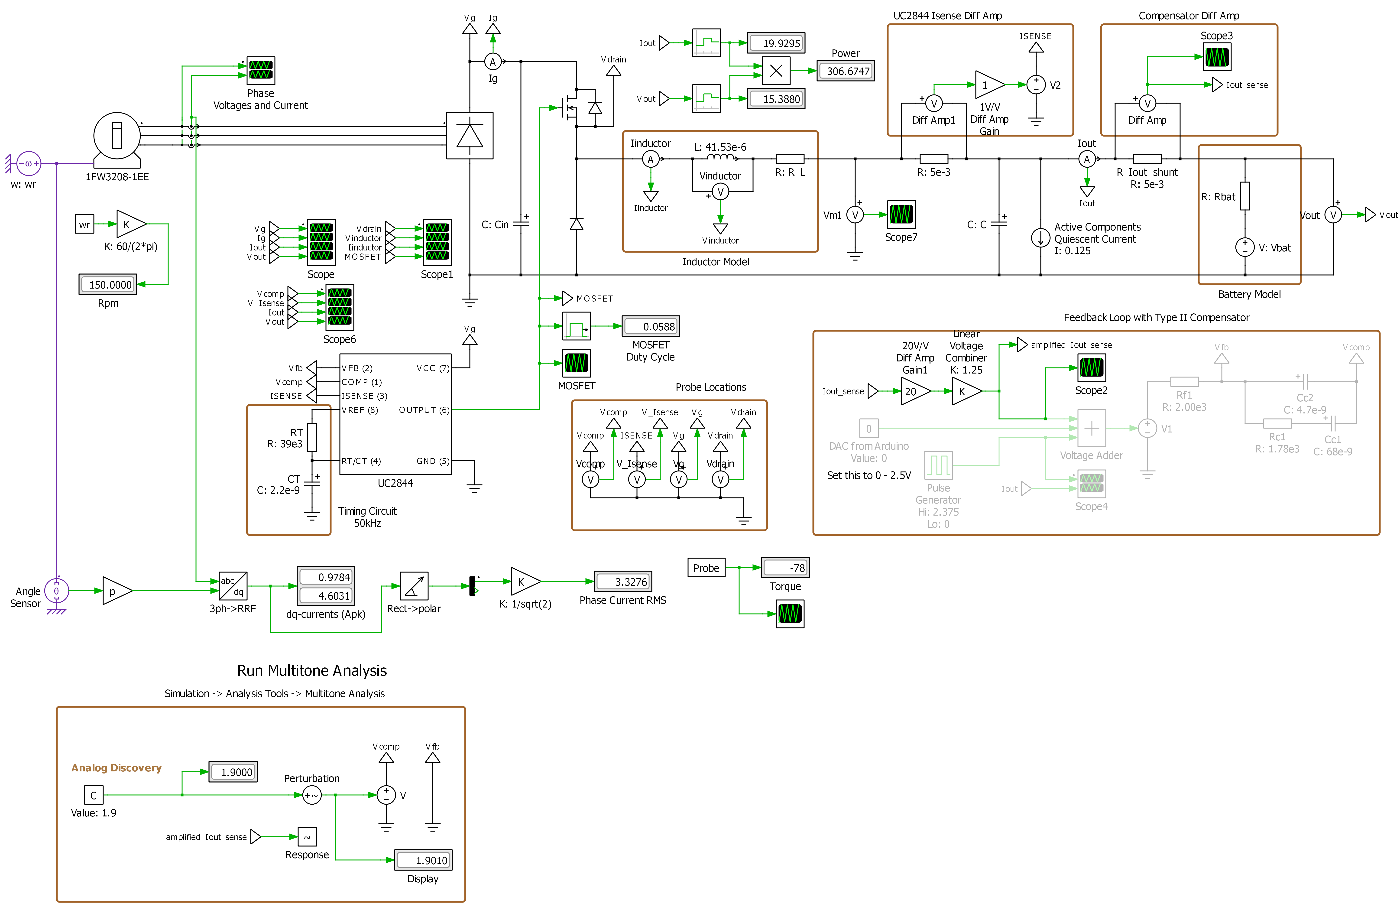
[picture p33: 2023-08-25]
large_wind_turbine/large_turbine_buck_converter_parameters/schematics/v3/frequency_experiment_9a.png

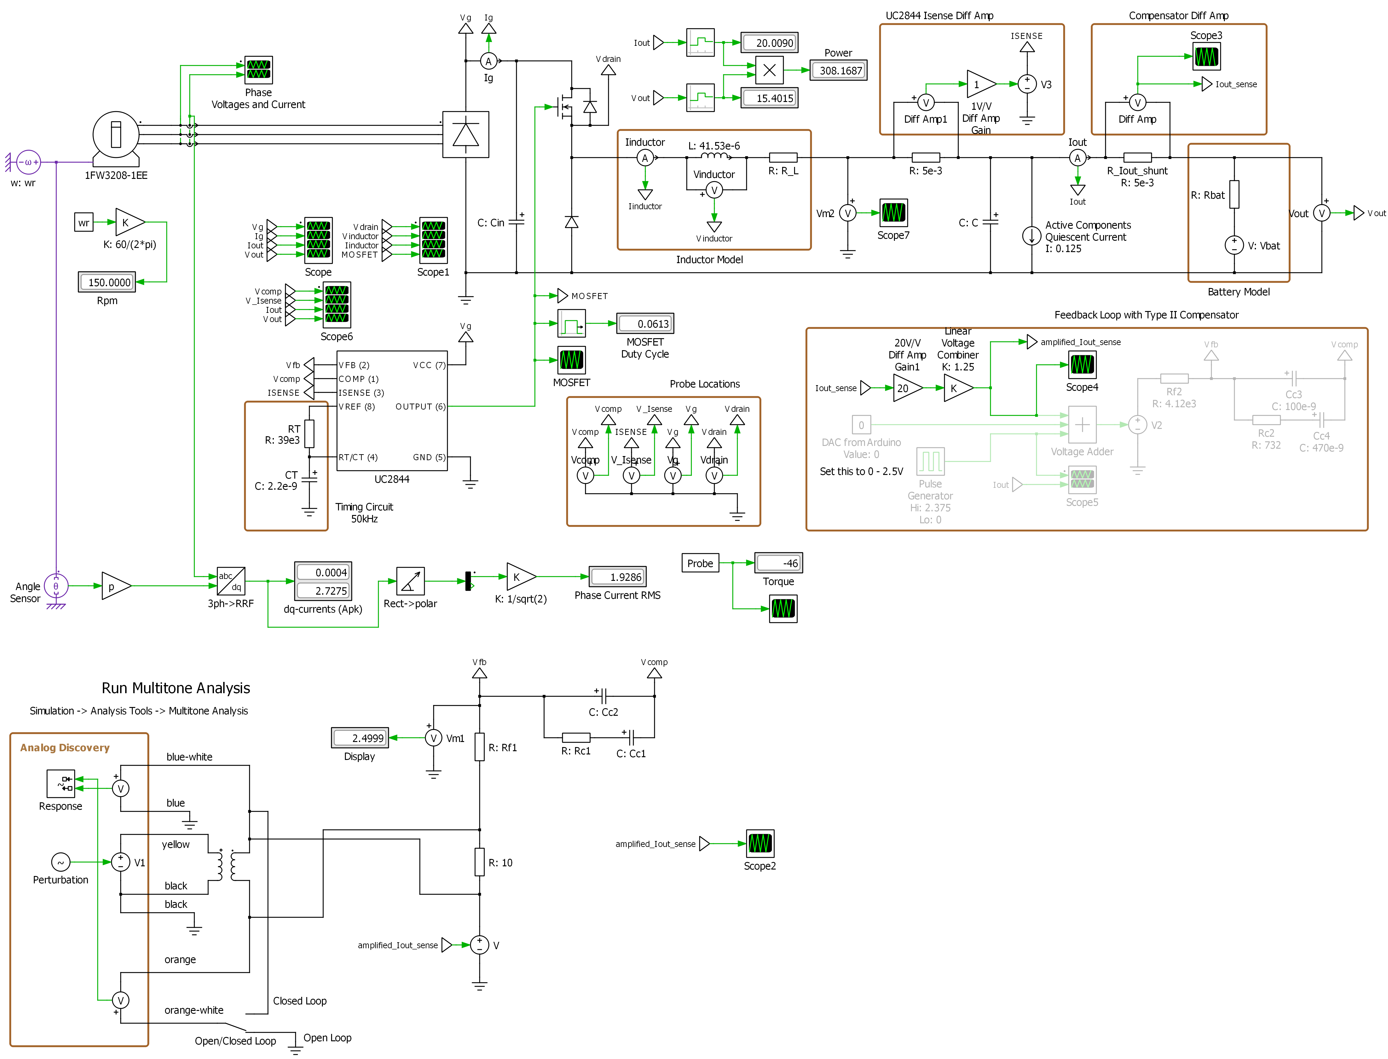
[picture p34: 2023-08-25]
large_wind_turbine/large_turbine_buck_converter_parameters/schematics/v3/frequency_experiment_10a.png

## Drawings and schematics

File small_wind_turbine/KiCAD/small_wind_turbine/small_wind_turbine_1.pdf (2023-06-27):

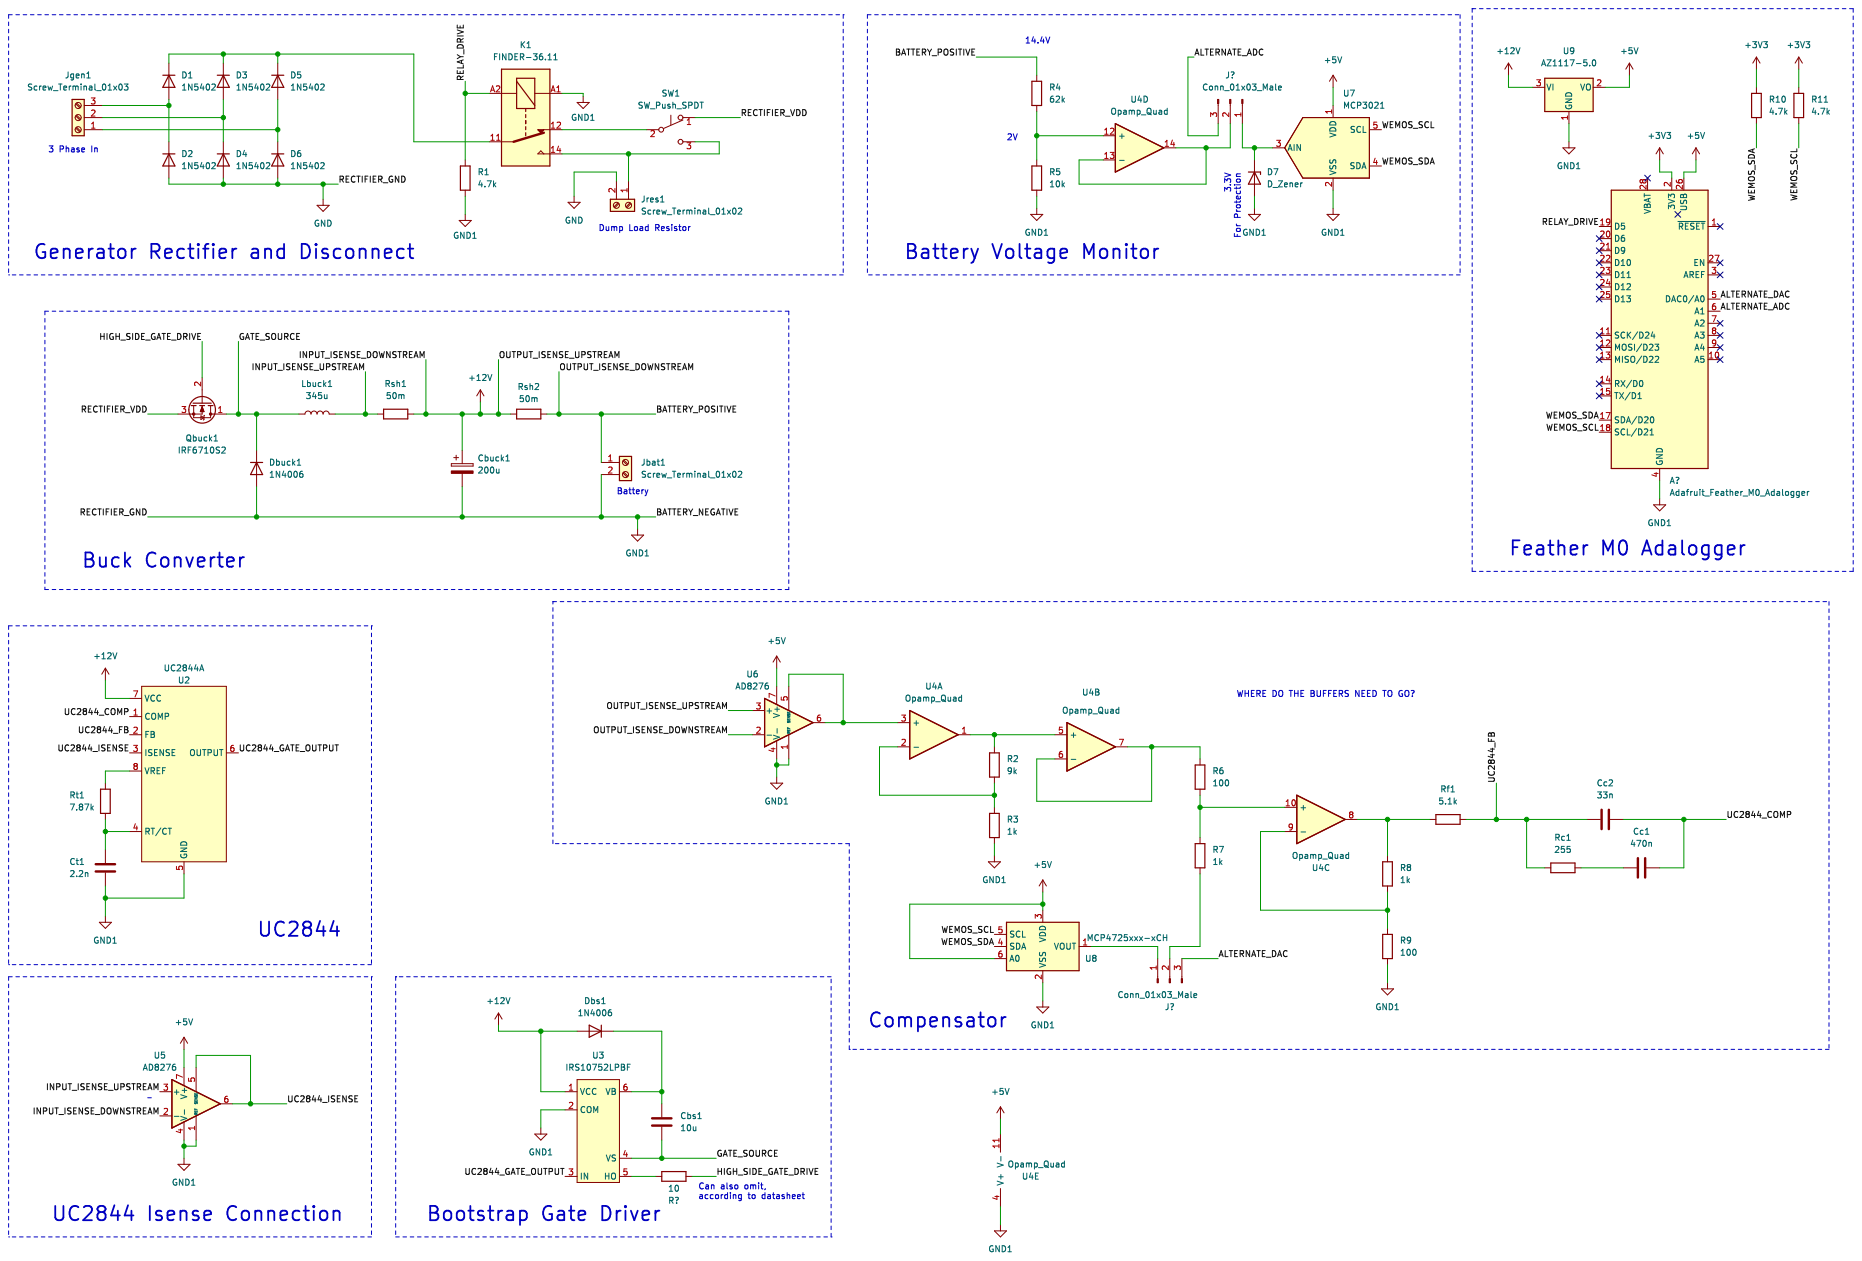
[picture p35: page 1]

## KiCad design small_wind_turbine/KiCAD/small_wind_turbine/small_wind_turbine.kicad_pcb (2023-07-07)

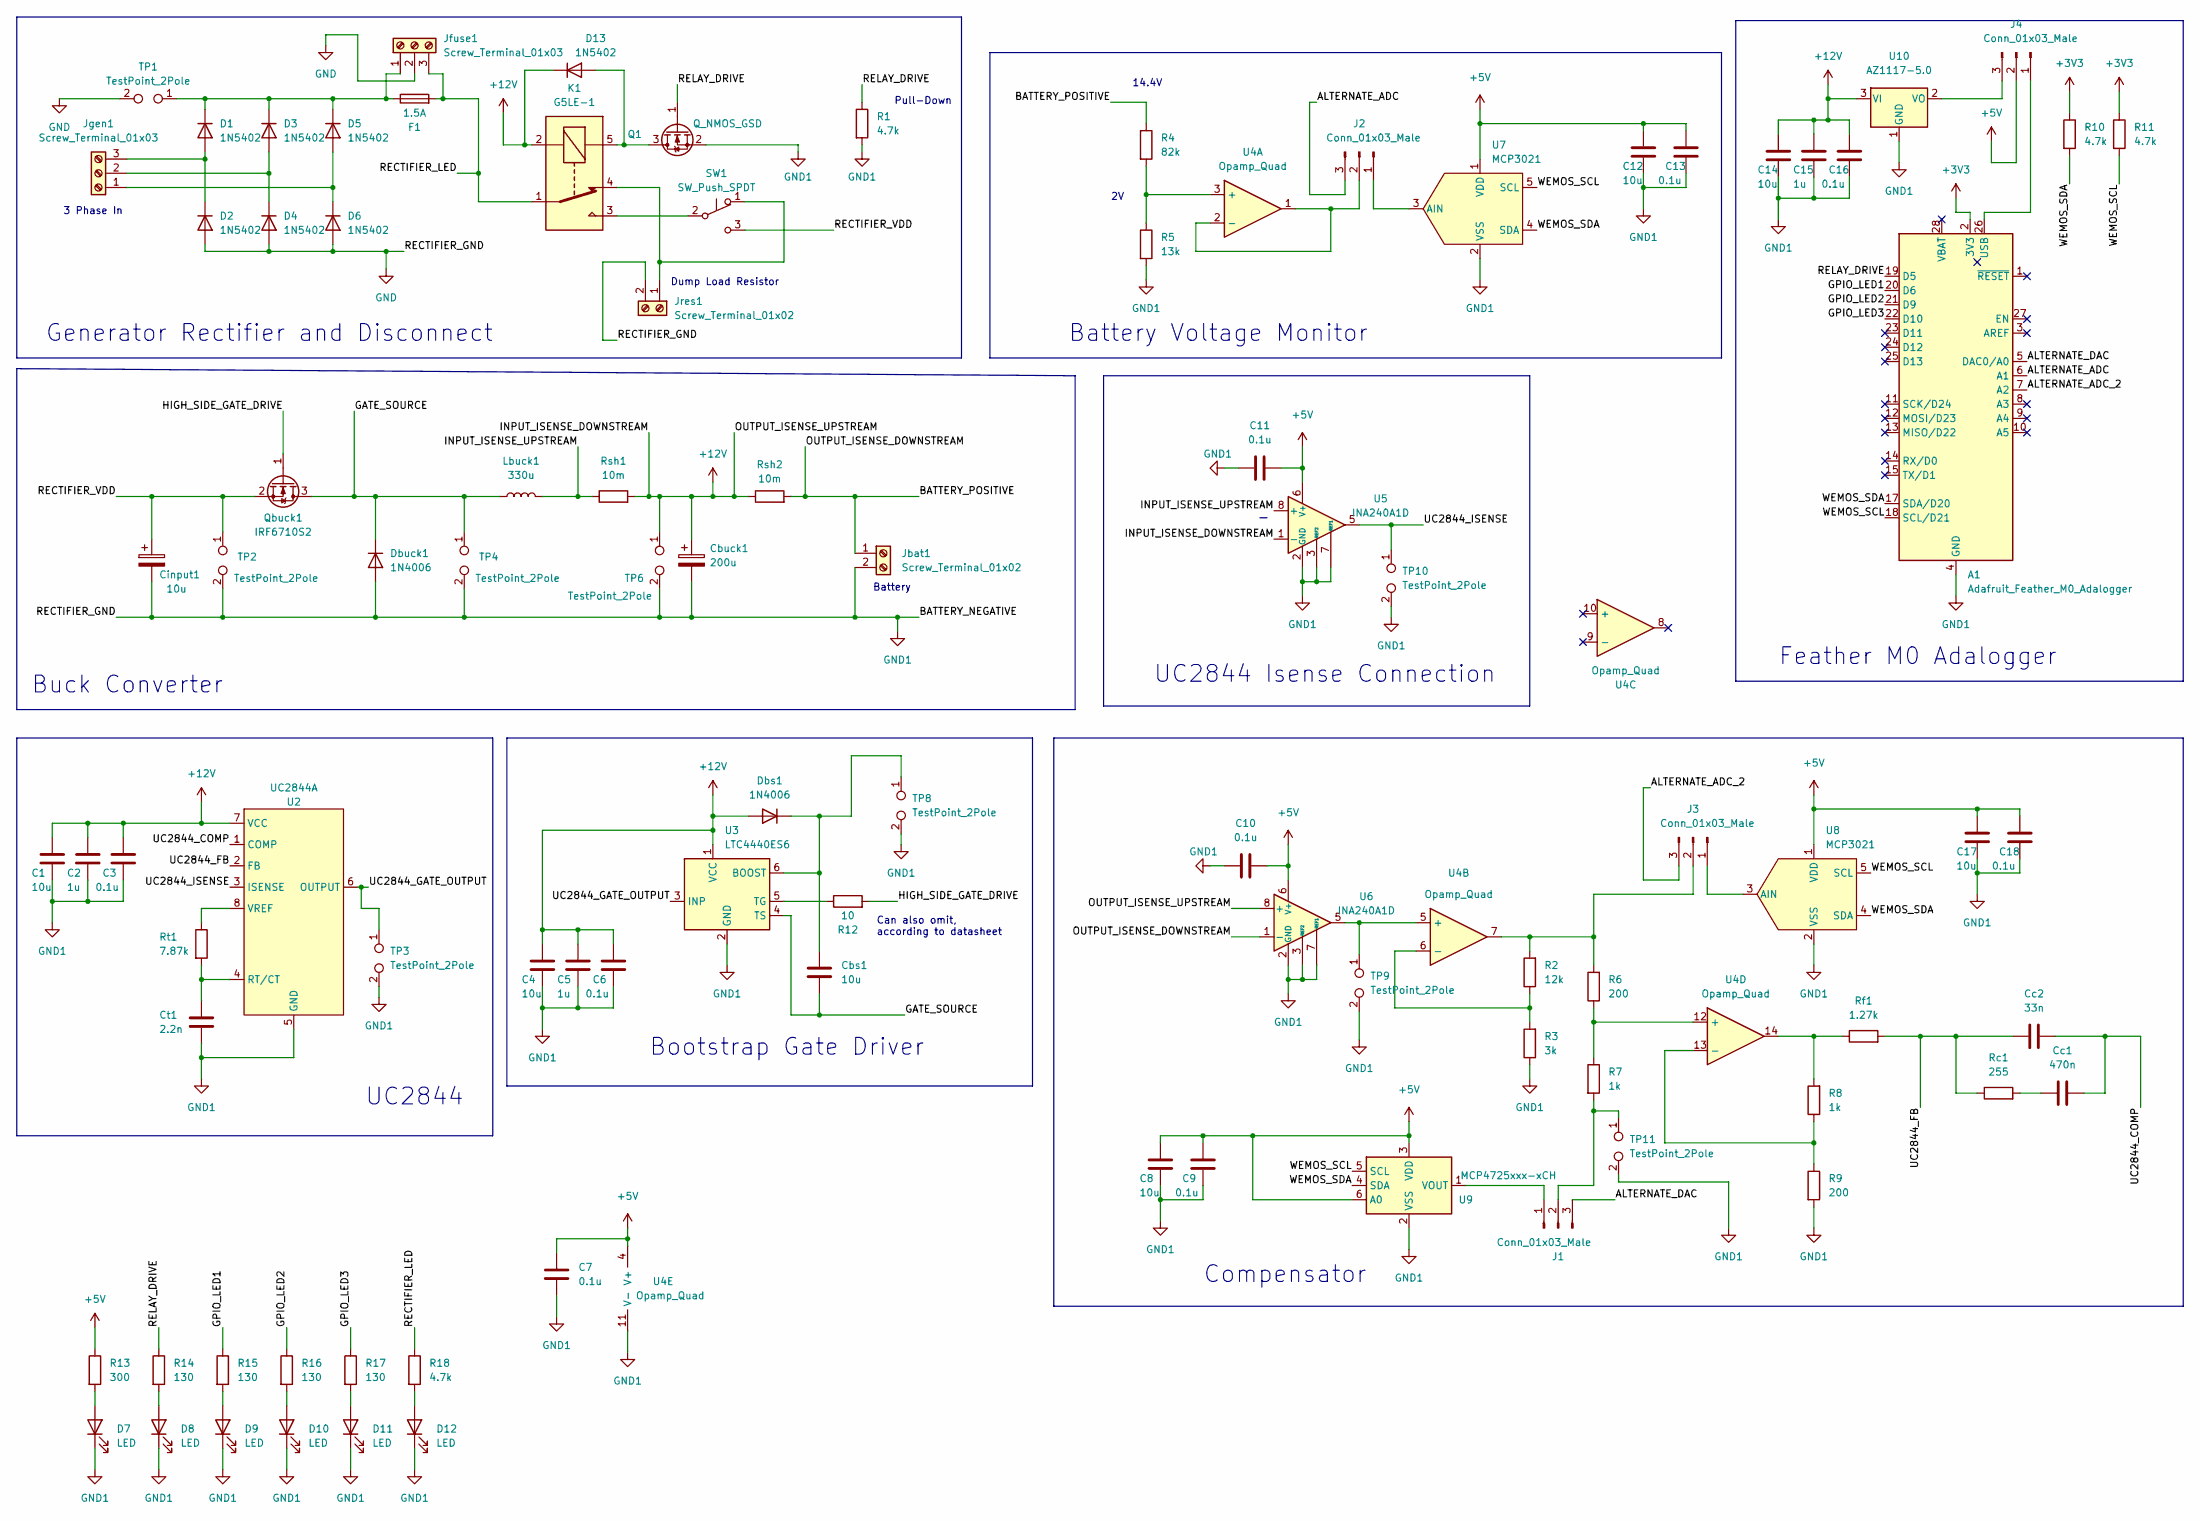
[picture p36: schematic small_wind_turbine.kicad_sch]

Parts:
A1: Adafruit_Feather_M0_Adalogger; Adafruit_Feather
C1, C4, C8, C12, C14, C17: 10u; C_0805_2012Metric
C2, C5, C15: 1u; C_0805_2012Metric
C3, C6, C7, C9, C10, C11, C13, C16, C18: 0.1u; C_0805_2012Metric
Cbs1: 10u; CP_Radial_D8.0mm_P3.50mm
Cbuck1: 200u; CP_Radial_D12.5mm_P5.00mm
Cc1: 470n; C_0805_2012Metric
Cc2: 33n; C_0805_2012Metric
Cinput1: 10u; CP_Radial_D6.3mm_P2.50mm
Ct1: 2.2n; C_0805_2012Metric
D1, D2, D3, D4, D5, D6: 1N5402; TO-277A_custom
D7, D8, D9, D10, D11, D12: LED; LED_0603_1608Metric
D13: 1N5402; SOD-323-EP_custom
Dbs1: 1N4006; TO-277A_custom
Dbuck1: 1N4006; TO-277A_custom
F1: 1.5A; FUSE_4527
J1, J2, J3, J4: Conn_01x03_Male; PinHeader_1x03_P2.54mm_Vertical
Jbat1: Screw_Terminal_01x02; CUI_TBP01R1-508-02BE
Jfuse1: Screw_Terminal_01x03; CUI_TBP01R1-508-03BE_no_extra
Jgen1: Screw_Terminal_01x03; CUI_TBP01R1-508-03BE
Jres1: Screw_Terminal_01x02; CUI_TBP01R1-508-02BE
K1: G5LE-1; Relay_SPDT_Omron_G5LE-1
Lbuck1: 330u; smd_inductor
Q1: Q_NMOS_GSD; SOT-23
Qbuck1: IRF6710S2; TO-220-3_Vertical
R1, R10, R11, R18: 4.7k; R_0805_2012Metric
R2: 12k; R_0805_2012Metric
R3: 3k; R_0805_2012Metric
R4: 82k; R_0805_2012Metric
R5: 13k; R_0805_2012Metric
R6, R9: 200; R_0805_2012Metric
R7, R8: 1k; R_0805_2012Metric
R12: 10; R_0805_2012Metric
R13: 300; R_0805_2012Metric
R14, R15, R16, R17: 130; R_0805_2012Metric
Rc1: 255; R_0805_2012Metric
Rf1: 1.27k; R_0805_2012Metric
Rsh1, Rsh2: 10m; R_1206_3216Metric
Rt1: 7.87k; R_0805_2012Metric
SW1: SW_Push_SPDT; manual_switch
TP1, TP2, TP3, TP4, TP6, TP8, TP9, TP10, TP11: TestPoint_2Pole; Oscilloscope_Test_Point
U2: UC2844A; SOIC-8_3.9x4.9mm_P1.27mm
U3: LTC4440ES6; SOT-23-6
U4: Opamp_Quad; SOIC-14_3.9x8.7mm_P1.27mm
U5, U6: INA240A1D; SOIC-8_3.9x4.9mm_P1.27mm
U7, U8: MCP3021; SOT-23-5
U9: MCP4725xxx-xCH; SOT-23-6
U10: AZ1117-5.0; SOT-223-3_TabPin2

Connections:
+3V3: A1.2 (3V3), R10.1, R11.1
+5V: C7.1, C8.1, C9.1, C10.2, C11.2, C12.1, C13.1, C17.1, C18.1, J4.2, R13.1, U4.4 (V+), U5.6 (V+), U6.6 (V+), U7.1 (VDD), U8.1 (VDD), U9.3 (VDD), U9.6 (A0)
+12V: C1.1, C2.1, C3.1, C4.1, C5.1, C6.1, C14.1, C15.1, C16.1, Cbuck1.1, D13.1 (K), Dbs1.2 (A), K1.2, Rsh1.2, Rsh2.1, TP6.1, U2.7 (VCC), U3.1 (VCC), U5.1 (-), U6.8 (+), U10.3 (VI)
/ALTERNATE_ADC: A1.6 (A1), J2.3
/ALTERNATE_ADC_2: A1.7 (A2), J3.3
/ALTERNATE_DAC: A1.5 (DAC0/A0), J1.3
/BATTERY_POSITIVE: Jbat1.1, R4.1, Rsh2.2, U6.1 (-)
/GATE_SOURCE: Cbs1.2, Dbuck1.1 (K), Lbuck1.1, Qbuck1.3 (D), TP4.1, U3.4 (TS)
/GPIO_LED1: A1.20 (D6), R15.1
/GPIO_LED2: A1.21 (D9), R16.1
/GPIO_LED3: A1.22 (D10), R17.1
/HIGH_SIDE_GATE_DRIVE: Qbuck1.1 (G), R12.2
/INPUT_ISENSE_UPSTREAM: Lbuck1.2, Rsh1.1, U5.8 (+)
/RECTIFIER_LED: F1.2, Jfuse1.3, K1.1, R18.1
/RECTIFIER_VDD: Cinput1.1, Qbuck1.2 (S), SW1.3 (C), TP2.1
/RELAY_DRIVE: A1.19 (D5), Q1.1 (G), R1.1, R14.1
/UC2844_COMP: Cc1.2, Cc2.1, U2.1 (COMP)
/UC2844_FB: Cc2.2, Rc1.1, Rf1.2, U2.2 (FB)
/UC2844_GATE_OUTPUT: TP3.1, U2.6 (OUTPUT), U3.3 (INP)
/UC2844_ISENSE: TP10.1, U2.3 (ISENSE), U5.5
/WEMOS_SCL: A1.18 (SCL/D21), R11.2, U7.5 (SCL), U8.5 (SCL), U9.5 (SCL)
/WEMOS_SDA: A1.17 (SDA/D20), R10.2, U7.4 (SDA), U8.4 (SDA), U9.4 (SDA)
GND: A1.4 (GND), A1.16 (GND), C1.2, C2.2, C3.2, C4.2, C5.2, C6.2, C7.2, C8.2, C9.2, C10.1, C11.1, C12.2, C13.2, C14.2, C15.2, C16.2, C17.2, C18.2, Cbuck1.2, Cinput1.2, Ct1.2, D2.2 (A), D4.2 (A), D6.2 (A), D7.1 (K), D8.1 (K), D9.1 (K), D10.1 (K), D11.1 (K), D12.1 (K), Dbuck1.2 (A), Jbat1.2, Jfuse1.2, Jres1.2, Q1.2 (S), R1.2, R3.1, R5.2, R9.2, TP1.2, TP2.2, TP3.2, TP4.2, TP6.2, TP8.2, TP9.2, TP10.2, TP11.2, U2.5 (GND), U3.2 (GND), U4.11 (V-), U5.2 (GND), U5.3 (REF2), U5.4 (GND), U5.7 (REF1), U6.2 (GND), U6.3 (REF2), U6.4 (GND), U6.7 (REF1), U7.2 (VSS), U8.2 (VSS), U9.2 (VSS), U10.1 (GND)
unnamed: A1.26 (USB), J4.1
unnamed: Cbs1.1, Dbs1.1 (K), TP8.1, U3.6 (BOOST)
unnamed: Cc1.1, Rc1.2
unnamed: Ct1.1, Rt1.2, U2.4 (RT/CT)
unnamed: D1.1 (K), D3.1 (K), D5.1 (K), F1.1, Jfuse1.1, TP1.1
unnamed: D1.2 (A), D2.1 (K), Jgen1.3
unnamed: D3.2 (A), D4.1 (K), Jgen1.2
unnamed: D5.2 (A), D6.1 (K), Jgen1.1
unnamed: D7.2 (A), R13.2
unnamed: D8.2 (A), R14.2
unnamed: D9.2 (A), R15.2
unnamed: D10.2 (A), R16.2
unnamed: D11.2 (A), R17.2
unnamed: D12.2 (A), R18.2
unnamed: D13.2 (A), K1.5, Q1.3 (D)
unnamed: J1.1, U9.1 (VOUT)
unnamed: J1.2, R7.2, TP11.1
unnamed: J2.1, U7.3 (AIN)
unnamed: J2.2, U4.1, U4.2 (-)
unnamed: J3.1, U8.3 (AIN)
unnamed: J3.2, R2.2, R6.2, U4.7
unnamed: J4.3, U10.2 (VO)
unnamed: Jres1.1, K1.4, SW1.1 (A)
unnamed: K1.3, SW1.2 (B)
unnamed: R2.1, R3.2, U4.6 (-)
unnamed: R4.2, R5.1, U4.3 (+)
unnamed: R6.1, R7.1, U4.12 (+)
unnamed: R8.1, R9.1, U4.13 (-)
unnamed: R8.2, Rf1.1, U4.14
unnamed: R12.1, U3.5 (TG)
unnamed: Rt1.1, U2.8 (VREF)
unnamed: TP9.1, U4.5 (+), U6.5

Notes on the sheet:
Bootstrap Gate Driver
Can also omit, according to datasheet
UC2844
14.4V
UC2844 Isense Connection
Pull-Down
Generator Rectifier and Disconnect
Compensator
Battery Voltage Monitor
Buck Converter
Battery
3 Phase In
Dump Load Resistor
Feather M0 Adalogger

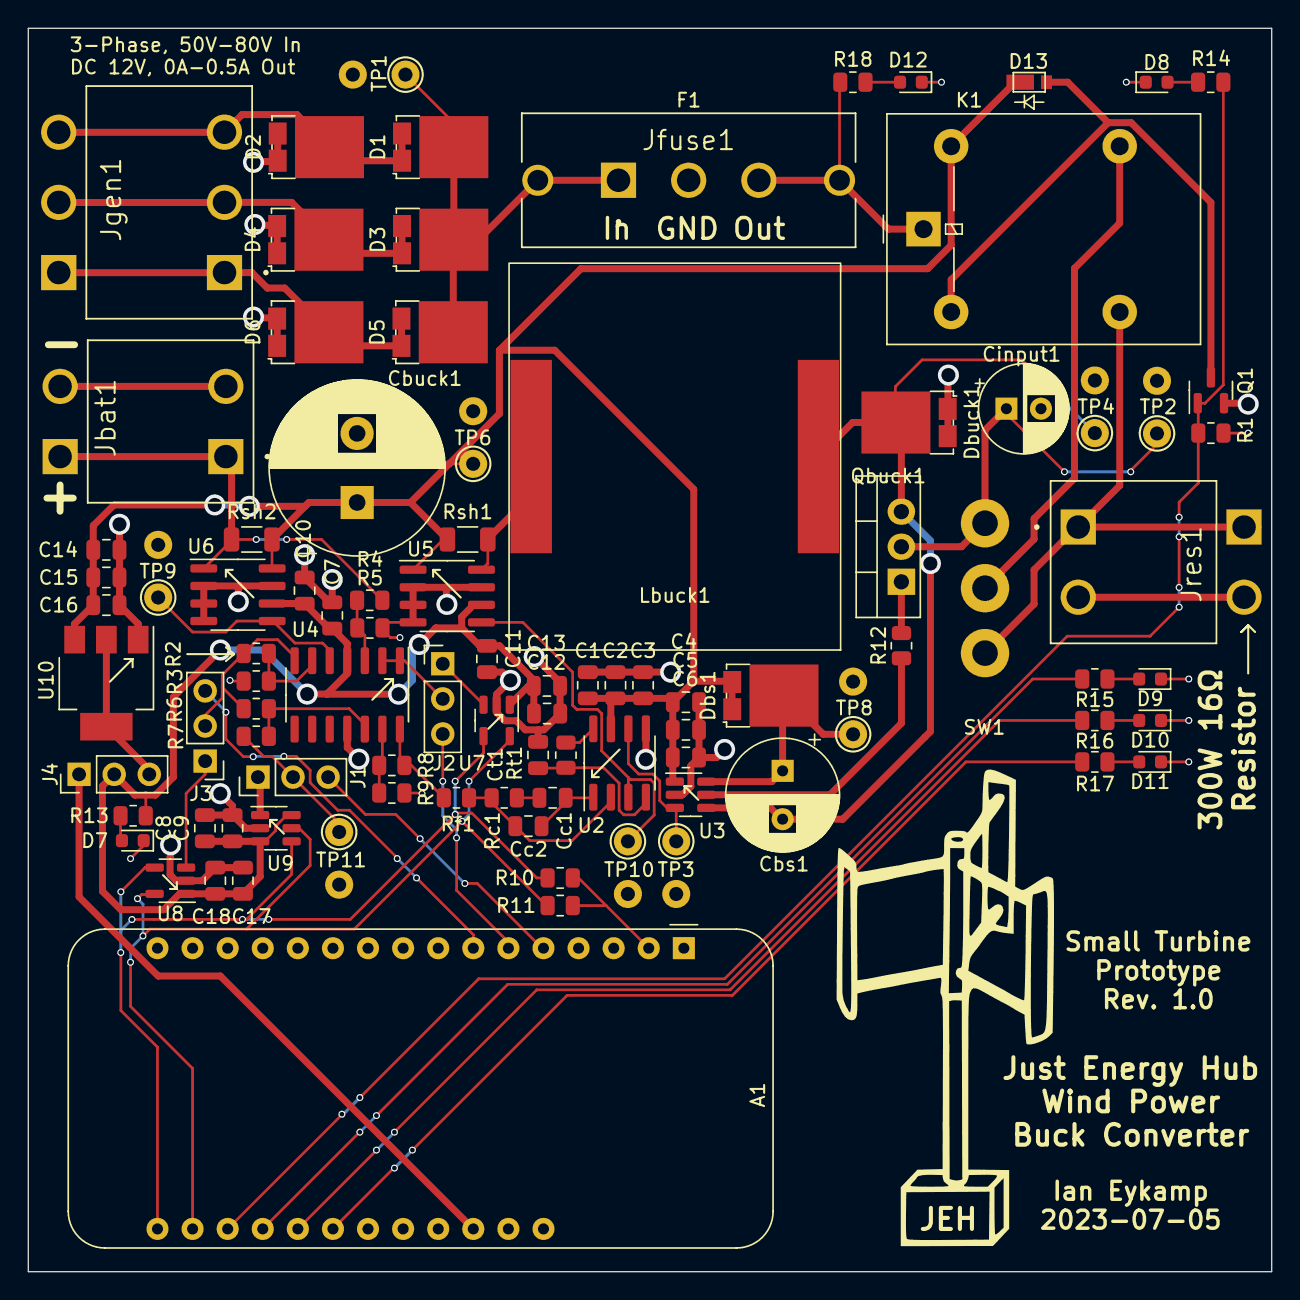
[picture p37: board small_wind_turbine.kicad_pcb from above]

Board: 2 copper layers, 90.0 x 90.0 mm, 97 parts (1 on the bottom side), 55 nets.

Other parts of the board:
Gen: LOGO; buck_converter_schematic_2
JEH: LOGO; h_rotor_design_3

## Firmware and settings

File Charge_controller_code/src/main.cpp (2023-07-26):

#include <Arduino.h>

#include <Wire.h>
#include "MCP3X21.h"
#include "MCP4716.hpp"

#define RELAY 5
#define LED_1 6
#define LED_2 9
#define LED_3 10
#define LED_ONBOARD_1 13
#define LED_ONBOARD_2 8

// initialize ADC
// according to the datasheet, the device address is given by
// 1001 followed by the custom device address, either 2 or 5
// in binary, this is 1001 010 and 1001 101
const uint16_t ADC_ref_voltage = 5 * 1000;  // in mV
const uint8_t ADC_address_02 = 0b1001010;
const uint8_t ADC_address_05 = 0b1001101;
const uint8_t DAC_address = 0b1100001; // 0x60;
MCP3021 battery_ADC(ADC_address_02);
MCP3021 current_ADC(ADC_address_05);
MCP4716 current_DAC(DAC_address);

void setup() {
  // put your setup code here, to run once:
  Serial.begin(115200);
  Serial.println("Hello World!");
  Wire.begin();
  battery_ADC.init();
  current_ADC.init();
  current_DAC.setGain(1);
  current_DAC.setVref(1);

  // set pin modes
  pinMode(RELAY, OUTPUT);
  pinMode(LED_1, OUTPUT);
  pinMode(LED_2, OUTPUT);
  pinMode(LED_3, OUTPUT);
  pinMode(LED_ONBOARD_1, OUTPUT);
  pinMode(LED_ONBOARD_2, OUTPUT);
  pinMode(A0, OUTPUT);

  // initialize all pins to low
  // digitalWrite(RELAY, HIGH);
  digitalWrite(RELAY, LOW);
  digitalWrite(LED_1, LOW);
  digitalWrite(LED_2, LOW);
  digitalWrite(LED_3, LOW);
  digitalWrite(LED_ONBOARD_1, LOW);
  digitalWrite(LED_ONBOARD_2, LOW);
}

void loop() {
  // Serial.println("Restarting Loop...");
  // digitalWrite(RELAY, HIGH);
  // delay(200);
  // digitalWrite(LED_1, HIGH);
  // delay(200);
  // digitalWrite(LED_2, HIGH);
  // delay(200);
  // digitalWrite(LED_3, HIGH);
  // delay(200);
  // digitalWrite(LED_ONBOARD_1, HIGH);
  // delay(200);
  // digitalWrite(LED_ONBOARD_2, HIGH);
  // delay(200);
  // digitalWrite(RELAY, LOW);
  // digitalWrite(LED_1, LOW);
  // digitalWrite(LED_2, LOW);
  // digitalWrite(LED_3, LOW);
  // digitalWrite(LED_ONBOARD_1, LOW);
  // digitalWrite(LED_ONBOARD_2, LOW);
  // delay(1000);

    current_DAC.setVout(int(1.25 * 1024 / 5));
    uint16_t raw_battery_voltage = battery_ADC.read();
    uint16_t raw_current_voltage = current_ADC.read();
    uint16_t battery_voltage = battery_ADC.toVoltage(raw_battery_voltage, ADC_ref_voltage);
    uint16_t current_voltage = current_ADC.toVoltage(raw_current_voltage, ADC_ref_voltage);
    uint16_t current = current_voltage / 0.010 / 20 / 5; // delta V / R / 20 gain / 5 gain

    Serial.print("Battery ADC: " + String(raw_battery_voltage) + ", voltage: " + String(battery_voltage) + "mV");
    Serial.print("  \t");
    Serial.println("Current ADC: " + String(raw_current_voltage) + ", voltage: " + String(current_voltage) + "mV, current = " + String(current) + "mA");
    // Serial.println();

    // current_DAC.setVout(int(0 * 1024 / 5));
    delay(500);

}

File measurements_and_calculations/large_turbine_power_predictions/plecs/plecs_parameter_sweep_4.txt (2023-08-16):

Kt =  24
Imax =  187

RL = 1ohms, wr = 50rpm, power = 3222.09W, voltage = 46.3002V
Kt =  24
Imax =  187

RL = 1ohms, wr = 100rpm, power = 5259.38W, voltage = 59.2225V
Kt =  24
Imax =  187

RL = 1ohms, wr = 150rpm, power = 5956.88W, voltage = 63.0179V
Kt =  24
Imax =  187

RL = 1ohms, wr = 200rpm, power = 6246.84W, voltage = 64.5422V
Kt =  24
Imax =  187

RL = 1ohms, wr = 250rpm, power = 6390.82W, voltage = 65.2698V
Kt =  24
Imax =  187

RL = 1ohms, wr = 300rpm, power = 6471.87W, voltage = 65.6855V
Kt =  24
Imax =  187

RL = 1.5ohms, wr = 50rpm, power = 3513.37W, voltage = 59.1593V
Kt =  24
Imax =  187

RL = 1.5ohms, wr = 100rpm, power = 6840.51W, voltage = 82.7343V
Kt =  24
Imax =  187

RL = 1.5ohms, wr = 150rpm, power = 8295.23W, voltage = 91.0782V
Kt =  24
Imax =  187

RL = 1.5ohms, wr = 200rpm, power = 8962.32W, voltage = 94.6807V
Kt =  24
Imax =  187

RL = 1.5ohms, wr = 250rpm, power = 9308.81W, voltage = 96.4792V
Kt =  24
Imax =  187

RL = 1.5ohms, wr = 300rpm, power = 9508.52W, voltage = 97.5117V
Kt =  24
Imax =  187

RL = 2ohms, wr = 50rpm, power = 3477.14W, voltage = 67.9155V
Kt =  24
Imax =  187

RL = 2ohms, wr = 100rpm, power = 7802.04W, voltage = 102.04V
Kt =  24
Imax =  187

RL = 2ohms, wr = 150rpm, power = 10136.9W, voltage = 116.258V
Kt =  24
Imax =  187

RL = 2ohms, wr = 200rpm, power = 11322.9W, voltage = 122.883V
Kt =  24
Imax =  187

RL = 2ohms, wr = 250rpm, power = 11971.2W, voltage = 126.337V
Kt =  24
Imax =  187

RL = 2ohms, wr = 300rpm, power = 12355.5W, voltage = 128.351V
Kt =  24
Imax =  187

RL = 2.5ohms, wr = 50rpm, power = 3310.84W, voltage = 74.0622V
Kt =  24
Imax =  187

RL = 2.5ohms, wr = 100rpm, power = 8296.81W, voltage = 117.656V
Kt =  24
Imax =  187

RL = 2.5ohms, wr = 150rpm, power = 11505.5W, voltage = 138.477V
Kt =  24
Imax =  187

RL = 2.5ohms, wr = 200rpm, power = 13306.6W, voltage = 148.933V
Kt =  24
Imax =  187

RL = 2.5ohms, wr = 250rpm, power = 14346.1W, voltage = 154.629V
Kt =  24
Imax =  187

RL = 2.5ohms, wr = 300rpm, power = 14981.9W, voltage = 158.018V
Kt =  24
Imax =  187

RL = 3ohms, wr = 50rpm, power = 3103.45W, voltage = 78.5254V
Kt =  24
Imax =  187

RL = 3ohms, wr = 100rpm, power = 8469.47W, voltage = 130.227V
Kt =  24
Imax =  187

RL = 3ohms, wr = 150rpm, power = 12458.7W, voltage = 157.852V
Kt =  24
Imax =  187

RL = 3ohms, wr = 200rpm, power = 14917.9W, voltage = 172.74V
Kt =  24
Imax =  187

RL = 3ohms, wr = 250rpm, power = 16418W, voltage = 181.209V
Kt =  24
Imax =  187

RL = 3ohms, wr = 300rpm, power = 17366.6W, voltage = 186.368V
Kt =  24
Imax =  187

RL = 3.5ohms, wr = 50rpm, power = 2892.8W, voltage = 81.8705V
Kt =  24
Imax =  187

RL = 3.5ohms, wr = 100rpm, power = 8433.29W, voltage = 140.365V
Kt =  24
Imax =  187

RL = 3.5ohms, wr = 150rpm, power = 13068.4W, voltage = 174.622V
Kt =  24
Imax =  187

RL = 3.5ohms, wr = 200rpm, power = 16181.1W, voltage = 194.314V
Kt =  24
Imax =  187

RL = 3.5ohms, wr = 250rpm, power = 18186W, voltage = 206V
Kt =  24
Imax =  187

RL = 3.5ohms, wr = 300rpm, power = 19498.4W, voltage = 213.298V
Kt =  24
Imax =  187

RL = 4ohms, wr = 50rpm, power = 2693.97W, voltage = 84.4486V
Kt =  24
Imax =  187

RL = 4ohms, wr = 100rpm, power = 8268.8W, voltage = 148.588V
Kt =  24
Imax =  187

RL = 4ohms, wr = 150rpm, power = 13406.3W, voltage = 189.077V
Kt =  24
Imax =  187

RL = 4ohms, wr = 200rpm, power = 17131.8W, voltage = 213.742V
Kt =  24
Imax =  187

RL = 4ohms, wr = 250rpm, power = 19660.7W, voltage = 228.981V
Kt =  24
Imax =  187

RL = 4ohms, wr = 300rpm, power = 21374.6W, voltage = 238.743V
Kt =  24
Imax =  187

RL = 4.5ohms, wr = 50rpm, power = 2512.06W, voltage = 86.484V
Kt =  24
Imax =  187

RL = 4.5ohms, wr = 100rpm, power = 8030.18W, voltage = 155.312V
Kt =  24
Imax =  187

RL = 4.5ohms, wr = 150rpm, power = 13536.7W, voltage = 201.52V
Kt =  24
Imax =  187

RL = 4.5ohms, wr = 200rpm, power = 17811.7W, voltage = 231.157V
Kt =  24
Imax =  187

RL = 4.5ohms, wr = 250rpm, power = 20860.9W, voltage = 250.177V
Kt =  24
Imax =  187

RL = 4.5ohms, wr = 300rpm, power = 22999.8W, voltage = 262.676V
Kt =  24
Imax =  187

RL = 5ohms, wr = 50rpm, power = 2347.88W, voltage = 88.1248V
Kt =  24
Imax =  187

RL = 5ohms, wr = 100rpm, power = 7752.64W, voltage = 160.859V
Kt =  24
Imax =  187

RL = 5ohms, wr = 150rpm, power = 13513.2W, voltage = 212.236V
Kt =  24
Imax =  187

RL = 5ohms, wr = 200rpm, power = 18262.7W, voltage = 246.722V
Kt =  24
Imax =  187

RL = 5ohms, wr = 250rpm, power = 21810.9W, voltage = 269.65V
Kt =  24
Imax =  187

RL = 5ohms, wr = 300rpm, power = 24384.5W, voltage = 285.097V
Kt =  24
Imax =  187

RL = 5.5ohms, wr = 50rpm, power = 2200.47W, voltage = 89.4712V
Kt =  24
Imax =  187

RL = 5.5ohms, wr = 100rpm, power = 7458.5W, voltage = 165.478V
Kt =  24
Imax =  187

RL = 5.5ohms, wr = 150rpm, power = 13378.5W, voltage = 221.482V
Kt =  24
Imax =  187

RL = 5.5ohms, wr = 200rpm, power = 18524.7W, voltage = 260.609V
Kt =  24
Imax =  187
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

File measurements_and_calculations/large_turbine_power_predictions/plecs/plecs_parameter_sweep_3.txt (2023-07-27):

Kt =  24
Imax =  187

RL = 1ohms, wr = 50rpm, power = 3222.09W
Kt =  24
Imax =  187

RL = 1ohms, wr = 100rpm, power = 5259.38W
Kt =  24
Imax =  187

RL = 1ohms, wr = 150rpm, power = 5956.88W
Kt =  24
Imax =  187

RL = 1ohms, wr = 200rpm, power = 6246.84W
Kt =  24
Imax =  187

RL = 1ohms, wr = 250rpm, power = 6390.83W
Kt =  24
Imax =  187

RL = 1ohms, wr = 300rpm, power = 6471.86W
Kt =  24
Imax =  187

RL = 1.2ohms, wr = 50rpm, power = 3397.59W
Kt =  24
Imax =  187

RL = 1.2ohms, wr = 100rpm, power = 5974.77W
Kt =  24
Imax =  187

RL = 1.2ohms, wr = 150rpm, power = 6951.19W
Kt =  24
Imax =  187

RL = 1.2ohms, wr = 200rpm, power = 7372.91W
Kt =  24
Imax =  187

RL = 1.2ohms, wr = 250rpm, power = 7585.93W
Kt =  24
Imax =  187

RL = 1.2ohms, wr = 300rpm, power = 7706.88W
Kt =  24
Imax =  187

RL = 1.4ohms, wr = 50rpm, power = 3490.48W
Kt =  24
Imax =  187

RL = 1.4ohms, wr = 100rpm, power = 6578.34W
Kt =  24
Imax =  187

RL = 1.4ohms, wr = 150rpm, power = 7867.18W
Kt =  24
Imax =  187

RL = 1.4ohms, wr = 200rpm, power = 8446.37W
Kt =  24
Imax =  187

RL = 1.4ohms, wr = 250rpm, power = 8744.34W
Kt =  24
Imax =  187

RL = 1.4ohms, wr = 300rpm, power = 8915.18W
Kt =  24
Imax =  187

RL = 1.6ohms, wr = 50rpm, power = 3523.79W
Kt =  24
Imax =  187

RL = 1.6ohms, wr = 100rpm, power = 7077.74W
Kt =  24
Imax =  187

RL = 1.6ohms, wr = 150rpm, power = 8703.24W
Kt =  24
Imax =  187

RL = 1.6ohms, wr = 200rpm, power = 9463.98W
Kt =  24
Imax =  187

RL = 1.6ohms, wr = 250rpm, power = 9863.01W
Kt =  24
Imax =  187

RL = 1.6ohms, wr = 300rpm, power = 10094.2W
Kt =  24
Imax =  187

RL = 1.8ohms, wr = 50rpm, power = 3515.02W
Kt =  24
Imax =  187

RL = 1.8ohms, wr = 100rpm, power = 7482.26W
Kt =  24
Imax =  187

RL = 1.8ohms, wr = 150rpm, power = 9459.37W
Kt =  24
Imax =  187

RL = 1.8ohms, wr = 200rpm, power = 10423.4W
Kt =  24
Imax =  187

RL = 1.8ohms, wr = 250rpm, power = 10939.4W
Kt =  24
Imax =  187

RL = 1.8ohms, wr = 300rpm, power = 11241.7W
Kt =  24
Imax =  187

RL = 2ohms, wr = 50rpm, power = 3477.14W
Kt =  24
Imax =  187

RL = 2ohms, wr = 100rpm, power = 7802.04W
Kt =  24
Imax =  187

RL = 2ohms, wr = 150rpm, power = 10136.9W
Kt =  24
Imax =  187

RL = 2ohms, wr = 200rpm, power = 11322.9W
Kt =  24
Imax =  187

RL = 2ohms, wr = 250rpm, power = 11971.2W
Kt =  24
Imax =  187

RL = 2ohms, wr = 300rpm, power = 12355.5W
Kt =  24
Imax =  187

RL = 2.2ohms, wr = 50rpm, power = 3419.6W
Kt =  24
Imax =  187

RL = 2.2ohms, wr = 100rpm, power = 8047.28W
Kt =  24
Imax =  187

RL = 2.2ohms, wr = 150rpm, power = 10738.4W
Kt =  24
Imax =  187

RL = 2.2ohms, wr = 200rpm, power = 12161.9W
Kt =  24
Imax =  187

RL = 2.2ohms, wr = 250rpm, power = 12956.9W
Kt =  24
Imax =  187

RL = 2.2ohms, wr = 300rpm, power = 13433.9W
Kt =  24
Imax =  187

RL = 2.4ohms, wr = 50rpm, power = 3349.24W
Kt =  24
Imax =  187

RL = 2.4ohms, wr = 100rpm, power = 8227.86W
Kt =  24
Imax =  187

RL = 2.4ohms, wr = 150rpm, power = 11267.1W
Kt =  24
Imax =  187

RL = 2.4ohms, wr = 200rpm, power = 12940.1W
Kt =  24
Imax =  187

RL = 2.4ohms, wr = 250rpm, power = 13895.1W
Kt =  24
Imax =  187

RL = 2.4ohms, wr = 300rpm, power = 14475.3W
Kt =  24
Imax =  187

RL = 2.6ohms, wr = 50rpm, power = 3270.95W
Kt =  24
Imax =  187

RL = 2.6ohms, wr = 100rpm, power = 8352.99W
Kt =  24
Imax =  187

RL = 2.6ohms, wr = 150rpm, power = 11727.1W
Kt =  24
Imax =  187

RL = 2.6ohms, wr = 200rpm, power = 13658.1W
Kt =  24
Imax =  187

RL = 2.6ohms, wr = 250rpm, power = 14784.9W
Kt =  24
Imax =  187

RL = 2.6ohms, wr = 300rpm, power = 15478.6W
Kt =  24
Imax =  187

RL = 2.8ohms, wr = 50rpm, power = 3188.2W
Kt =  24
Imax =  187

RL = 2.8ohms, wr = 100rpm, power = 8431.04W
Kt =  24
Imax =  187

RL = 2.8ohms, wr = 150rpm, power = 12122.7W
Kt =  24
Imax =  187

RL = 2.8ohms, wr = 200rpm, power = 14316.9W
Kt =  24
Imax =  187

RL = 2.8ohms, wr = 250rpm, power = 15625.9W
Kt =  24
Imax =  187

RL = 2.8ohms, wr = 300rpm, power = 16442.6W
Kt =  24
Imax =  187

RL = 3ohms, wr = 50rpm, power = 3103.45W
Kt =  24
Imax =  187

RL = 3ohms, wr = 100rpm, power = 8469.47W
Kt =  24
Imax =  187

RL = 3ohms, wr = 150rpm, power = 12458.7W
Kt =  24
Imax =  187

RL = 3ohms, wr = 200rpm, power = 14917.9W
Kt =  24
Imax =  187

RL = 3ohms, wr = 250rpm, power = 16418W
Kt =  24
Imax =  187

RL = 3ohms, wr = 300rpm, power = 17366.5W
Kt =  24
Imax =  187

RL = 3.2ohms, wr = 50rpm, power = 3018.41W
Kt =  24
Imax =  187

RL = 3.2ohms, wr = 100rpm, power = 8474.87W
Kt =  24
Imax =  187

RL = 3.2ohms, wr = 150rpm, power = 12739.6W
Kt =  24
Imax =  187

RL = 3.2ohms, wr = 200rpm, power = 15463.2W
Kt =  24
Imax =  187

RL = 3.2ohms, wr = 250rpm, power = 17161.3W
Kt =  24
Imax =  187

RL = 3.2ohms, wr = 300rpm, power = 18249.9W
Kt =  24
Imax =  187

RL = 3.4ohms, wr = 50rpm, power = 2934.27W
Kt =  24
Imax =  187

RL = 3.4ohms, wr = 100rpm, power = 8452.94W
Kt =  24
Imax =  187

RL = 3.4ohms, wr = 150rpm, power = 12970.4W
Kt =  24
Imax =  187

RL = 3.4ohms, wr = 200rpm, power = 15954.7W
Kt =  24
Imax =  187
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

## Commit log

2023-06-14 initial commit from first three weeks
    [NewFile1.csv, NewFile2.csv, NewFile3.csv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]
2023-06-14 plot all transfer functions
    [compensator_bode.csv, plant_bode.csv]
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2023-06-15 finish buck converter analysis
    [square_wave_response.csv]
2023-06-15 plot unrectified generator data
    [100Ohm.csv, 4_5Ohm.csv, 6_8Ohm.csv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]
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2023-06-19 plot maximum power test oscilloscope data
    [NewFile1.csv, NewFile2.csv, NewFile3.csv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]
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2023-06-19 make copy of and rename buck converter parameter notebooks
    [closed_loop_bode.csv, compensator_bode.csv, open_loop_bode.csv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]
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2023-06-21 completely revamp folder structure
    [100Ohm.csv, 4_5Ohm.csv, 6_8Ohm.csv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]
2023-06-21 start KiCAD schematic and create UC2844A symbol
    [small_wind_turbine.kicad_pcb, small_wind_turbine.kicad_sch]
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2023-06-21 finish current sensing feedback circuit
    [small_wind_turbine.kicad_sch]
2023-06-22 add high side gate driver and connect common grounds
    [small_wind_turbine.kicad_sch]
2023-06-22 wip schematic. Replace inverting adder with non-inverting adder. Postulate on replacing Isense resistor for UC2844
    [small_wind_turbine.kicad_sch]
2023-06-23 mostly update compensator values; slight mismatch with open loop transfer function
    [closed_loop_bode.csv, compensator_bode.csv, open_loop_bode.csv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]
2023-06-23 increase time step and play with compensator values
    [closed_loop_bode.csv, open_loop_bode.csv]
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2023-06-25 compare old vs. new compensator values before and after compensating for discrepancy
    [closed_loop_bode_old.csv, compensator_bode.csv, compensator_bode_old.csv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]
2023-06-26 increase current to 500mA, re-run simulations, and it works! Also tidy up schematics
    [open_loop_bode_no_quiescent.csv, plant_bode.csv, plant_bode_no_quiescent.csv]
2023-06-26 update all plots and schematics in buck_converter_parameters.ipynb
    [closed_loop_bode.csv, closed_loop_bode_no_quiescent.csv, compensator_bode.csv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]
2023-06-26 re-organize plecs data csv and schematic files
    [closed_loop_bode.csv, closed_loop_bode_no_quiescent.csv, closed_loop_bode_old.csv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]
2023-06-26 clean up and annotate schematic
    [small_wind_turbine.kicad_sch]
2023-06-27 add gate resistor and source connection to gate driver
    [small_wind_turbine.kicad_sch]
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2023-06-29 after design review: calculate and add input capacitance
    [small_wind_turbine.kicad_sch]
2023-06-29 remove extra low-side switch and shunt
    [small_wind_turbine.kicad_sch]
2023-06-29 substitute different diff amp with 20V/V gain
    [small_wind_turbine.kicad_sch]
2023-06-29 update KiCAD resistor values to match PLECS model
    [small_wind_turbine.kicad_sch]
2023-06-30 start adding footprints and bypass capacitors
    [small_wind_turbine.kicad_sch]
2023-06-30 finish assigning IC footprints and bypass capacitance. All IC footprints are double-checked.
    [small_wind_turbine.kicad_sch]
2023-06-30 wip assigning passives footprints
    [small_wind_turbine.kicad_sch]
2023-06-30 wip adding footprints (2)
    [small_wind_turbine.kicad_sch]
2023-06-30 wip adding footprints (3)
    [small_wind_turbine.kicad_sch]
2023-06-30 wip adding footprints (4)
    [small_wind_turbine.kicad_sch]
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2023-06-30 add test points galore
    [small_wind_turbine.kicad_pcb, small_wind_turbine.kicad_sch]
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2023-07-04 move test points close to proper locations
    [small_wind_turbine.kicad_pcb, small_wind_turbine.kicad_sch]
2023-07-04 finalize relative positions; ready to start finessing
    [small_wind_turbine.kicad_pcb, small_wind_turbine.kicad_sch]
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2023-07-04 wip laying traces (2)
    [small_wind_turbine.kicad_pcb]
2023-07-04 almost finished laying traces
    [small_wind_turbine.kicad_pcb]
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2023-07-04 finish connecting ground vias
    [small_wind_turbine.kicad_pcb]
2023-07-04 improve ground plane near relay
    [small_wind_turbine.kicad_pcb]
2023-07-05 replace terminal blocks and add silkscreen design
    [small_wind_turbine.kicad_pcb, small_wind_turbine.kicad_sch]
2023-07-05 replace 'Ohm' with Omega symbol
    [small_wind_turbine.kicad_pcb]
2023-07-05 add 3d models and fix transistor pin ordering
    [small_wind_turbine.kicad_pcb, small_wind_turbine.kicad_sch]
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2023-07-05 add jumper to switch 5V rail
    [small_wind_turbine.kicad_pcb, small_wind_turbine.kicad_sch]
2023-07-05 change position of J4 label
    [small_wind_turbine.kicad_pcb]
2023-07-06 fix Q1 pin ordering
    [small_wind_turbine.kicad_pcb, small_wind_turbine.kicad_sch]
2023-07-06 add optional fuse terminal block
    [small_wind_turbine.kicad_pcb, small_wind_turbine.kicad_sch]
2023-07-06 add relay protection flyback diode
    [small_wind_turbine.kicad_pcb, small_wind_turbine.kicad_sch]
2023-07-06 re-zip files for review (2)
    [small_wind_turbine.kicad_sch, small_wind_turbine_BOM.csv]
2023-07-07 download final bom from spreadsheet
    [Digikey_BOM.xlsx, closed_loop_bode.csv, compensator_bode.csv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]
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2023-07-10 first pass large wind turbine PLECS model; working control loop, slightly underdamped
    [closed_loop_bode.csv, compensator_bode.csv, open_loop_bode.csv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]
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2023-07-26 create parameter sweep of resistance and angular velocity of generator in PLECS
    [plecs_parameter_sweep.txt, plecs_parameter_sweep_2.txt]
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2023-07-27 re-run plecs model, add assumptions, and submit report
    [plecs_parameter_sweep_3.txt]
2023-08-16 update parameter sweep simulation script and calculate dump load voltage
    [plecs_parameter_sweep_4.txt]
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2023-08-17 move internal_resistance.ipynb to archive and small_buck_converter_design_calculations.ipynb to small_wind_turbine folder
    [100Ohm.csv, 4_5Ohm.csv, 6_8Ohm.csv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]
2023-08-25 create new version of large buck converter calculations with correctly performing control loop
    [closed_loop_bode.csv, compensator_bode.csv, open_loop_bode.csv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]
